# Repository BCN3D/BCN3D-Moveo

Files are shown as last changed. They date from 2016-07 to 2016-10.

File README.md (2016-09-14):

#BCN3D MOVEO

This is the repository that contains the CAD files, the STL files, the user manual (with the assembly manual), the firmware, and the Bill of Materials of the BCN3D Moveo.
BCN3D Technologies keeps taking important steps in order to achieve his goal of bringing the digital manufacturing technology to everyone. In this occasion we are presenting the BCN3D Moveo, a robotic arm design from scratch and developed by our engineers in collaboration with the Departament d’Ensenyament from the Generalitat de Catalunya. Its structure is fully printed using additive manufacturing technologies and its electronics are controlled by the software Arduino.
Moveo, fully functional nowadays, has been born, as all the BCN3D Technologies products, with an open and educational wish.

##Why BCN3D Moveo

One of the Departament d’Ensenyament worries is the high price of the materials the grade students must use on their internships. Holding that in mind, an Open Source robotic arm, adaptable by the students and low cost reproducible could take several educational itineraries: mechanical design, automatism, industrial programing, etc.
Thus, the BCN3D Moveo should allow the educational centers to enjoy a modifiable and easily accessible for the students, at a price far lower than the usual industrial equipment they used to have to acquire, with enough output for training purposes.
As a Fundació CIM area, BCN3D Technologies shares its educational vocation. That is the reason why when the Departament d’Ensenyament contacted us in order to suggest and offer this project a year ago we didn’t hesitate on taking that opportunity.
Once we had the robotic arm designed and manufactured we started the last phase of the project, which consisted on an assembling and fine tuning workshop for 15 institutes around Catalonia, which took place in the BCN3D Technologies.
These institutes already have the BCN3D Moveo in their classrooms and workshops, and will have to present an internship program that proves their knowledge about the arm during September.

##Open Source Technology: Github

As we have done with all our developed produtcs, the BCN3D Moveo files will be available for everyone. Thanks to the platform Github, a website where users around the world share their designs, anyone will be able to obtain all the necessary information in order to assemble his own BCN3D Moveo at home.

Unlike the other BCN3D products, the Moveo won’t be commercialized. The project has been born and developed in order to make a move for the community progress starting from the Departament d’Ensenyament idea.
Nevertheless, BCN3D will fee all the Moveo know how on our Github account, as we have been doing with all the BCN3D Technologies products. Thus, the users will be able to find the bill of material (BOM), where all the needed components for the assembling of the arm come detailed, as the CAD designs, so anyone will be able to modify the BCN3D Moveo design as they wish.
Furthermore, the Github users will find the STL files for the structure printing and the assembling, fine tuning and firmware upload manuals, which will be available both in English and Spanish.

## Acknowledgements

This project is based on a project by [Andreas Hölldorfer](http://chaozlabs.blogspot.de/). You can see his original project on [Hackaday.io](https://hackaday.io/project/3800-3d-printable-robot-arm), [Github](https://github.com/4ndreas/BetaBots-Robot-Arm-Project/tree/master), [Youtube](https://www.youtube.com/channel/UCeFKz1UJUd5YuxS1ZikqYwA).

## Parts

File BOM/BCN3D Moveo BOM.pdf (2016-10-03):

BCN3D Moveo BOM.xlsx

1

BOM ID | BOM | QUANTITY
1 | Stepper Motor SM42HT47-1684 1,8º step, 1,6 A, 3600 g·cm | 1
2 | ARDUINO MEGA 2560 | 1
3 | Stepper Driver tb6560 | 6
4 | Power Supply 24V 320W | 1
5 | RAMPS V1.4 | 1
6 | Power converter 24V a 12V | 1
7 | Servo Motor 180§ 55G TORQUE=13KG/CM | 1
8 | Gear Ratio 5:1 Planetary Gearbox Nema 17 Stepper 17HS19-1684S-PG5 ( step 0,35º , 2Nm, 1,68A) | 1
9 | Nema 23, 112mm, Ø8mm flat shaft SM57HT112-3004A, step 1,8º, 3A,28Kg·cm | 2
10 | Stepper Motor SM35HT36-1004A, 1,8º step, 1A, 1400g·cm | 1
11 | Stepper Motor nema 17 SM42HT33-1334, 1,8º step, 1,33A, 2200 g·cm | 1
12 | Chrome steel smooth bar-134mm | 1
13 | Chrome steel smooth bar-114mm | 1
14 | Chrome steel smooth bar-80mm | 1
15 | Ball Bearing 608ZZ 8mm x 22mm x 7mm | 10
16 | Ball Bearing 625ZZ 5mm x 16mm x 5mm | 8
17 | Ball Bearing 624ZZ 4mm x 13mm x 5mm | 9
18 | Ball Bearing 623ZZ 3mm x 10mm x 4mm | 3
19 | Brass insert M4 | 3
20 | Brass insert M3 | 20
21 | Pulley T5, Bore 8mm, 14 tooth, 17mm width | 3
22 | Pulley T5, Bore 5mm, 10 tooth, 17 mm width | 2
23 | ROD BAR M8 L 42mm | 1
24 | ZCOUPLING STEEL 5 TO 8 mm rigid | 1
25 | Axial Fan DC 24V 80x80mm | 1
26 | Axial Fan DC 24V 50x50mm | 1
27 | Powwer supply cable IEC 1,8m | 1
28 | Cable USB 2.0 AM/BM 1,8m | 1
29 | Cable Ties | 10
30 | Selfoil bearing 5mm x 8mm x 10mm | 8
31 | Selfoil bearing 8mm x 12mm x 20mm | 2
32 | Wood Base - 550mm x 550mm x 16mm | 1
33 | Breco belt T5, 16mm width, L 180cm | 1,8 m
101 | Dimension A: M-3 Dimension B: 10 mm | 30
102 | Dimension A: M-3 Dimension B: 12 mm | 6
103 | Dimension A: M-3 Dimension B: 16 mm | 13
104 | Dimension A: M-3 Dimension B: 20 mm | 4
105 | Dimension A: M-3 Dimension B: 25 mm | 5
106 | Dimension A: M-3 Dimension B: 30 mm | 2
107 | Dimension A: M-3 Dimension B: 40 mm | 7
108 | Dimension A: M-4 Dimension B: 12 mm | 2
109 | Dimension A: M-4 Dimension B: 10 mm | 2
110 | Dimension A: M-4 Dimension B: 16 mm | 8
111 | Dimension A: M-4 Dimension B: 40 mm | 4
112 | Dimension A: M-4 Dimension B: 45 mm | 6
113 | Dimension A: M-4 Dimension B: 60 mm | 4
114 | Dimension A: M-5 Dimension B: 14 mm | 120
115 | Dimension A: M-5 Dimension B: 20 mm | 8
116 | Dimension A: M-8 Dimension B: 65 mm | 1
117 | Dimension A: M-4 Dimension B: 25 mm | 4
118 | Dimension A: M-3 Nut | 30
119 | Dimension A: M-4 Nut | 4
120 | Dimension A: M-4 Locknut | 18
121 | Dimension A: M-5 Locknut | 16
122 | Dimension A: M-8 Locknut | 2

Components

Fasteners

BCN3D Moveo BOM.xlsx

2

123 | Dimension A: M-4 Dimension B: 20 mm | 3
124 | Dimension A: M-3 Dimension B: 8 mm | 4
125 | Dimension A: M-4 Dimension B: 30 mm | 8
126 | Dimension A: M-3 Dimension B: 35 mm | 4
127 | Washer M-3 | 10
| BOM ID | Parts | Name | Quantity
| 202 | Articulation 1 | 1M1 | 1
| 203 | | 1M2 | 1
| 204 | | 1M3 | 1
| 205 | Articulation 2 | 2M1 | 1
| 206 | | 2M2M | 1
| 207 | | 2M2H | 1
| 208 | | T2M1D | 1
| 209 | | T2M1I | 1
| 210 | Articulation 3 | 3M1 | 1
| 210A | | 3M2C | 1
| 211 | | 3M2 | 1
| 212 | | T3M1 | 1
| 213 | Articulation 4 | 4M1 | 1
| 214 | | 4M2 | 1
| 215 | | 4M2C | 1
| 216 | | T4M1 | 1
| 217 | Machine - tool | Top plate | 1
| 218 | | Bottom plate | 1
| 219 | | Cilinder | 2
| 220 | | Pivot arm | 1
| 221 | | Gripper left | 1
| 222 | | Gripper right | 1
| 223 | | Idol gear | 1
| 224 | | Servo gear | 1
| 225 | Box electronics | Box | 1
| 226 | | Fan module | 1
| 227 | | Suport Drivers | 1
| 228 | Base | Potes | 4
| 229 | Cover | Tapa 2M1 | 2
| 230 | | Tapa 3M1 | 2
| 231 | | Tapa 4M1 | 2
| 232 | | Tapa TBB | 1

Printed Parts

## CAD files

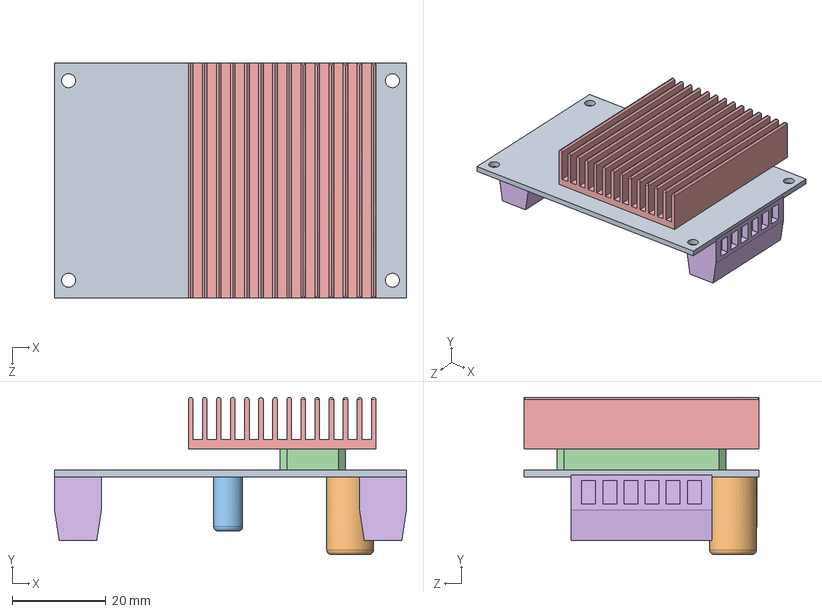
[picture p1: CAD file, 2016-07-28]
CAD files/Driver.SLDASM
75.0 x 33.5 x 50.0 mm
PCB TB6560
Capacitor 1
Capacitor 2
Chip
Sink
Terminal x 2

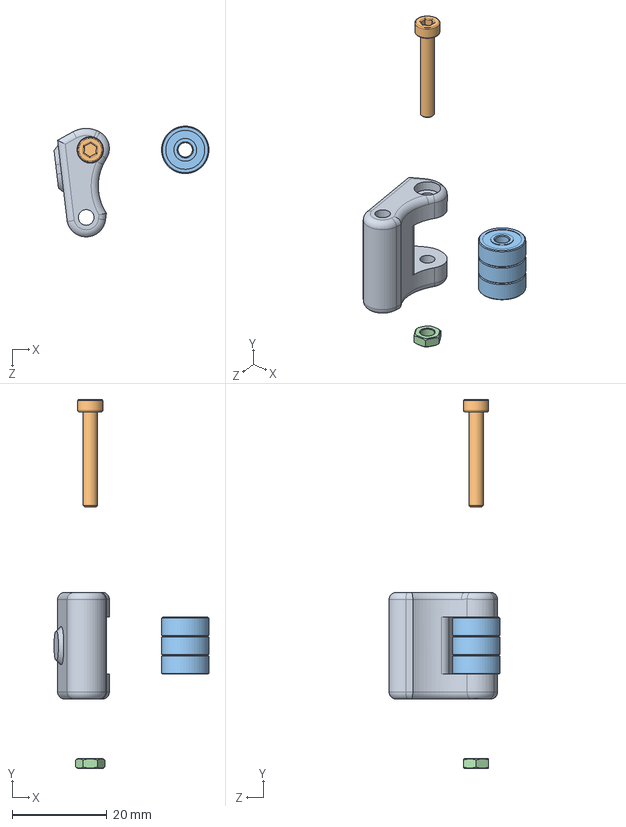
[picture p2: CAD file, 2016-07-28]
CAD files/M1 Tensor D.SLDASM
32.6 x 77.7 x 23.3 mm
T4M1E
M3x20
Bearing 3Bore 10Ext 4Height x 3
M3 Nut

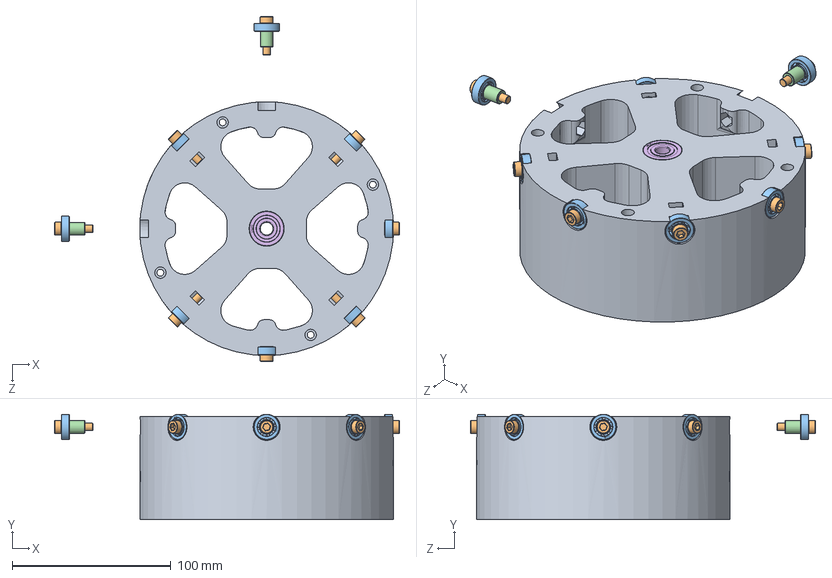
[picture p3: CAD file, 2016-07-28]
CAD files/Rotary Plate.SLDASM
217.5 x 66.5 x 217.5 mm
1M2A
M5x20 x 8
Bearing 5mm x 8
Spacer M5x10 x 8
Spacer M8x20
8mm Bearing x 2

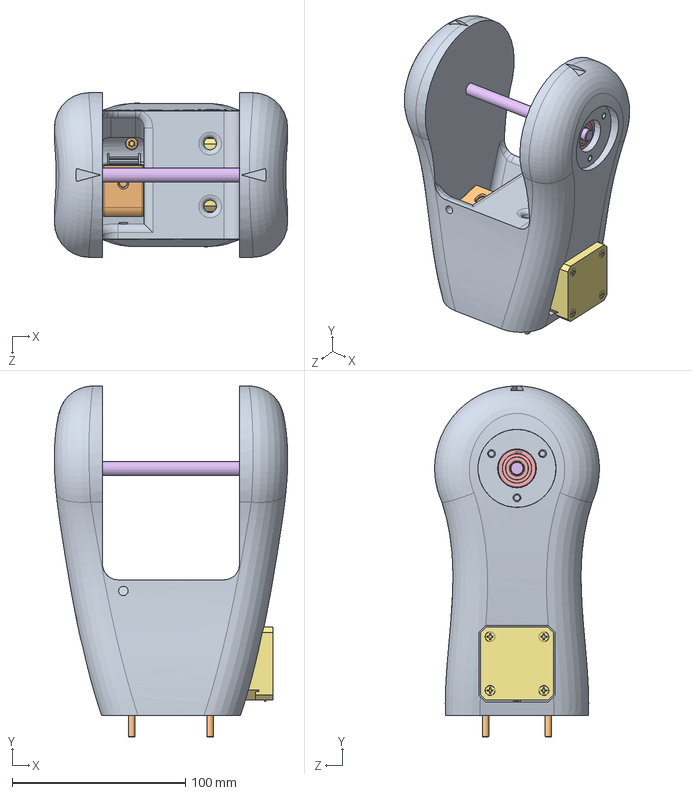
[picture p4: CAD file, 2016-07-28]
CAD files/3M1.SLDASM
134.6 x 202.4 x 95.0 mm
3M1D
T3M1C
M4 Nut
M4x20
Bearing 4Bore 13Ext 5 x 3
M3x40
Nema 17 Reductor
M3x12 x 4
Pulley 8mm IGNIS
M4x16 x 4
M3 Nut
Brass insert M3 x 6
8mm Bearing x 2
Smooth bar 8mm x 121mm

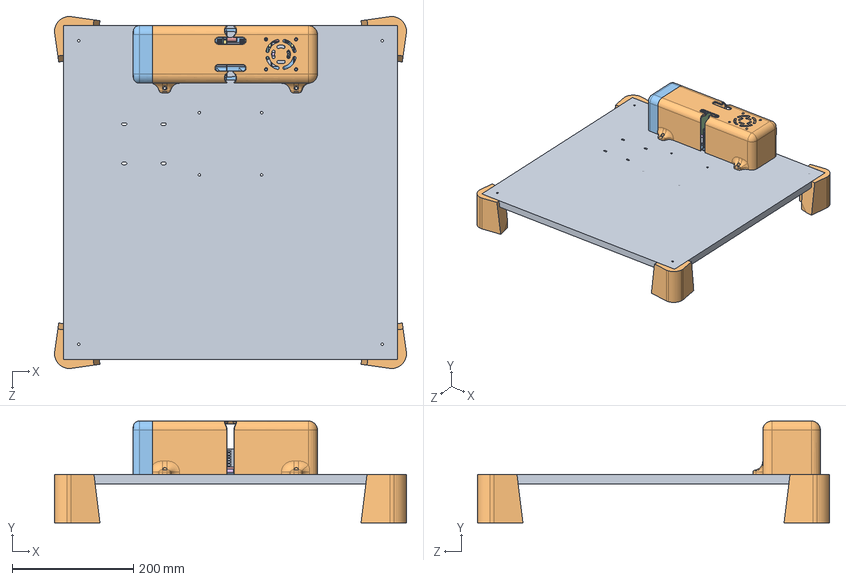
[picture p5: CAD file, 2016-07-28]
CAD files/Base assembly.SLDASM
579.8 x 168.0 x 579.8 mm
Base fusta
Potes base B x 4
Suport Drivers E
PCB TB6560 x 6
Capacitor 1 x 6
Capacitor 2 x 6
Chip x 6
Sink x 6
Terminal x 12
Box C
Fan Module
Fan

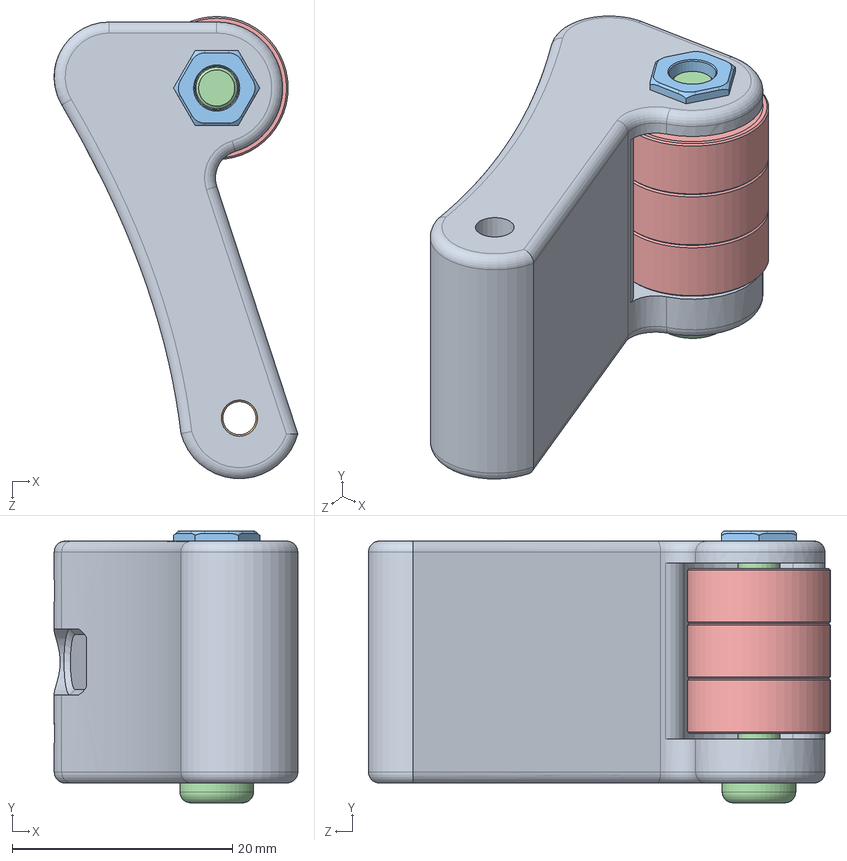
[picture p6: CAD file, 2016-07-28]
CAD files/Tensor I.SLDASM
22.2 x 24.7 x 42.0 mm
T2M1BI
M3 Nut
M4 Nut
M4x20
Bearing 4Bore 13Ext 5 x 3

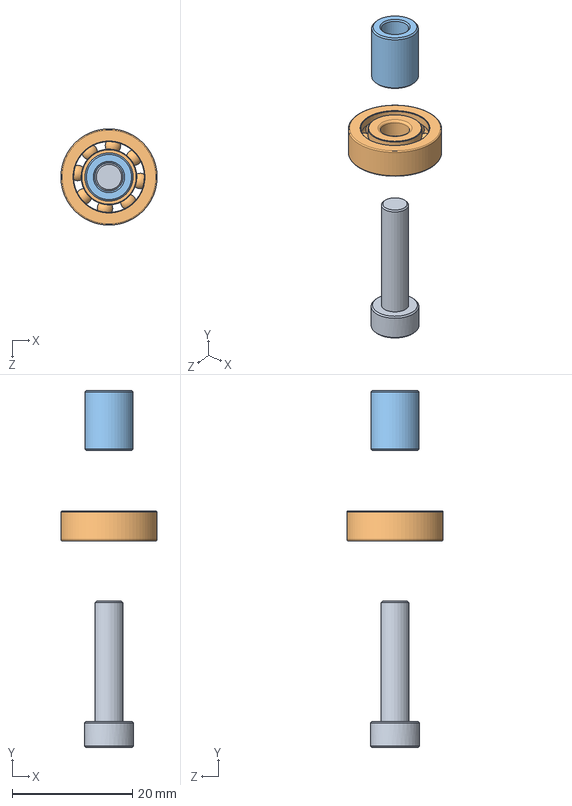
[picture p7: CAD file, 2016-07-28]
CAD files/Sistema rodaments.SLDASM
16.0 x 59.3 x 16.0 mm
M5x20
Bearing 5mm
Spacer M5x10

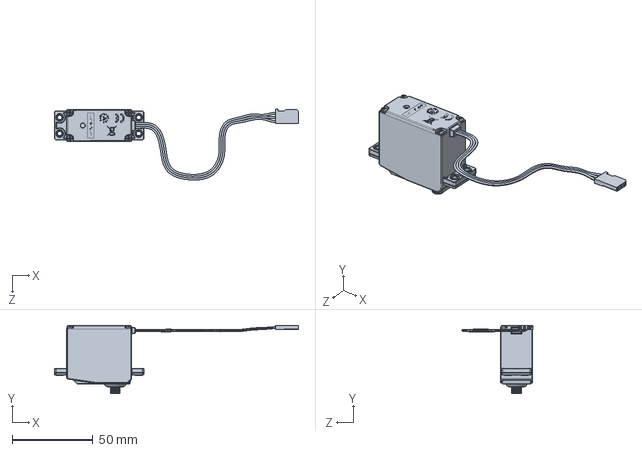
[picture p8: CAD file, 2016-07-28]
CAD files/2.SLDASM
151.2 x 42.3 x 44.1 mm

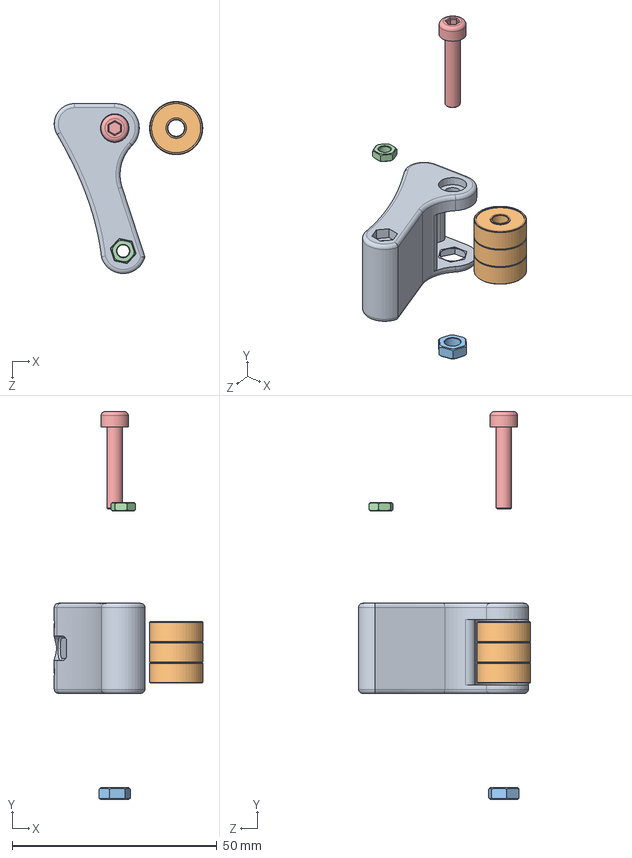
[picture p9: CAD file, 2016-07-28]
CAD files/Tensor D.SLDASM
36.3 x 94.7 x 42.0 mm
T2M1BD
Bearing 4Bore 13Ext 5 x 3
M4 Nut
M3 Nut
M4x20
Arandela

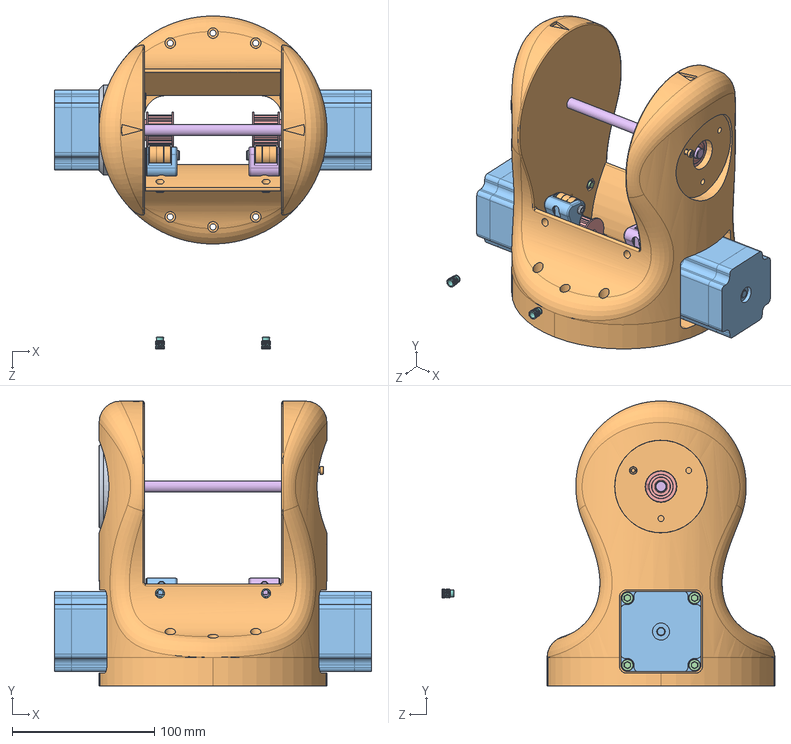
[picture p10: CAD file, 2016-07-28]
CAD files/2M1 assembly.SLDASM
222.5 x 200.0 x 233.7 mm
M5 Lock x 8
2M1D
Nema 23 x 2
M5x15 x 8
8mm Bearing x 2
T2M1BI
M3 Nut x 2
M4 Nut x 2
M4x20 x 2
Bearing 4Bore 13Ext 5 x 6
T2M1BD
Arandela
Pulley 8mm IGNIS x 2
Smooth bar 8mm x 140mm
Brass insert M4 x 2

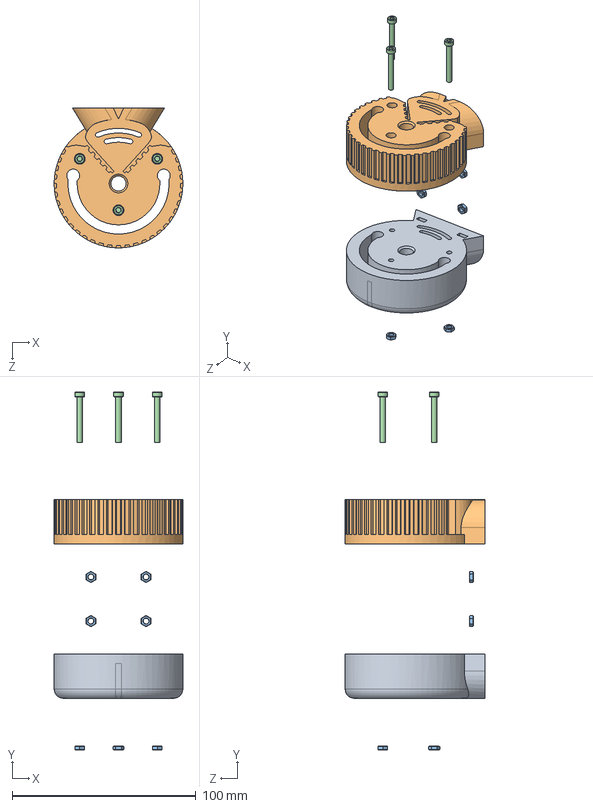
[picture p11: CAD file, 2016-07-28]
CAD files/4M2.SLDASM
70.0 x 194.7 x 76.0 mm
4M2B
4M2CB
M3 Nut x 7
M3x25 x 3

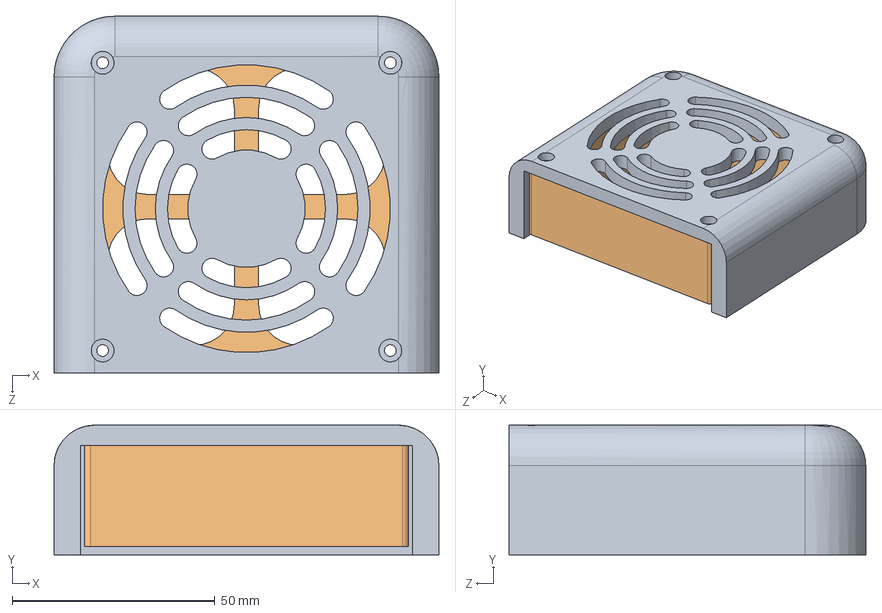
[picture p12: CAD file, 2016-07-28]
CAD files/Module Fan Assembly.SLDASM
95.0 x 32.0 x 88.0 mm
Fan Module
Fan

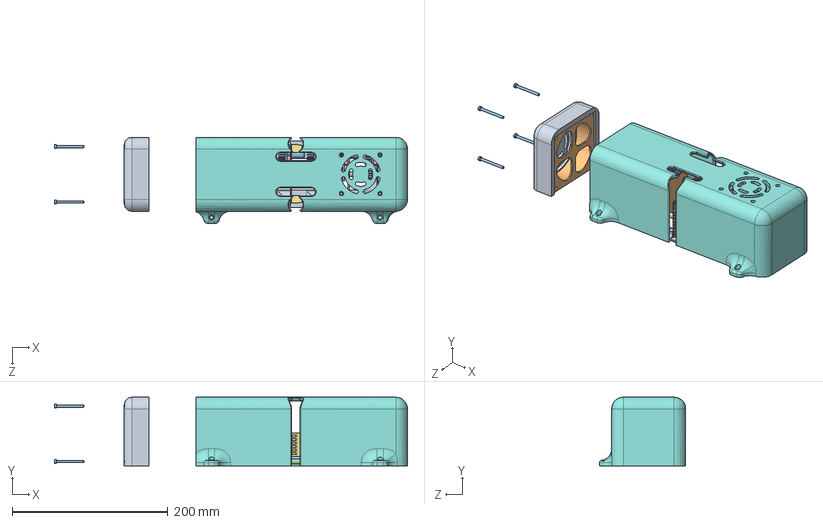
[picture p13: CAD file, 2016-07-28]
CAD files/Box Assembly B.SLDASM
453.0 x 88.0 x 111.0 mm
Suport Drivers E
PCB TB6560 x 6
Capacitor 1 x 6
Capacitor 2 x 6
Chip x 6
Sink x 6
Terminal x 12
Box C
Fan Module
Fan
M3x35 x 4

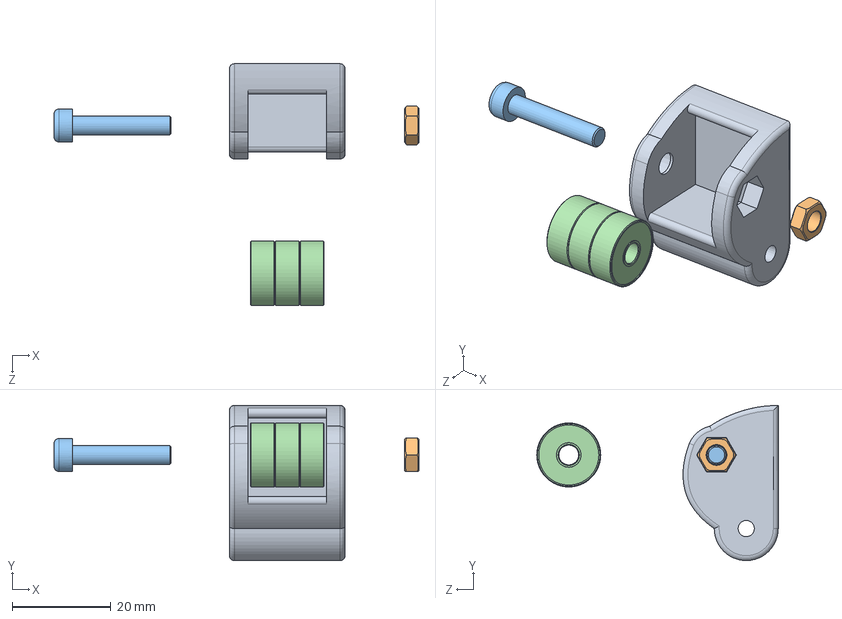
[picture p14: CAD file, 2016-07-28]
CAD files/T3M1.SLDASM
74.1 x 31.5 x 49.0 mm
T3M1C
M4 Nut
M4x20
Bearing 4Bore 13Ext 5 x 3

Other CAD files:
CAD files/2M2 assembly.SLDASM
CAD files/Drivers Support Assembly B.SLDASM
CAD files/2M2.SLDASM
CAD files/Gripper B Assembly.SLDASM
CAD files/1M1B.SLDPRT
CAD files/1M2A.SLDPRT
CAD files/1M3.SLDASM
CAD files/1M3A.SLDPRT
CAD files/2M1D.SLDPRT
CAD files/2M2HA.SLDPRT
CAD files/2M2M assembly.SLDASM
CAD files/2M2MA.SLDPRT
CAD files/3M2C.SLDPRT
CAD files/3M2CC.SLDPRT
CAD files/4M1D.SLDPRT
CAD files/4M2B.SLDPRT
CAD files/4M2CB.SLDPRT
CAD files/8mm Bearing.SLDPRT
CAD files/Arandela.SLDPRT
CAD files/Barra llisa 8mm x 80mm.SLDPRT
CAD files/Base fusta.SLDPRT
CAD files/Bearing 3Bore 10Ext 4Height.SLDPRT
CAD files/Bearing 4Bore 13Ext 5.SLDPRT
CAD files/Bearing 5mm.SLDPRT
CAD files/Bottom Plate C.SLDPRT
CAD files/Box C.SLDPRT
CAD files/Brass insert M3.SLDPRT
CAD files/Brass insert M4.SLDPRT
CAD files/Capacitor 1.SLDPRT
CAD files/Capacitor 2.SLDPRT
CAD files/Chip.SLDPRT
CAD files/Cilinder.SLDPRT
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

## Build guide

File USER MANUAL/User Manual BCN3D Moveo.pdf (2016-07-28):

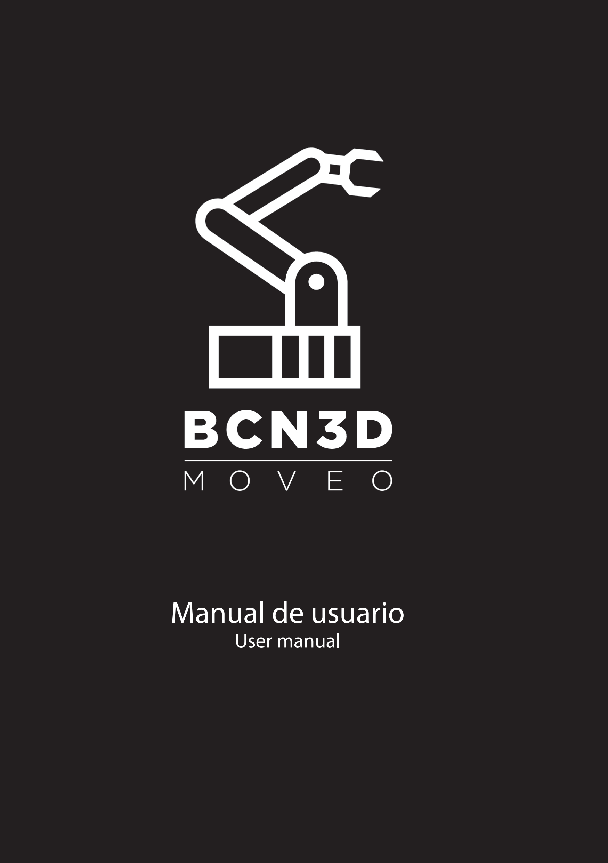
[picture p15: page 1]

# Manual de usuario

# User manual

2 - Manual de usuario User manual

Manual de montaje
Assembly manual

Manual de usuario User manual

¿Cómo usar el BCN3D Moveo? How to use the BCN3D Moveo?

Instalación del firmware
Firmware installation

Sobre el BCN3D Moveo
About de BCN3D Moveo

## ÍNDICE INDEX

3 - 4

6 - 39

40 - 42

43 - 45

Manual de usuario User manual - 3

## Sobre el BCN3D Moveo About the BCN3D Moveo

BCN3D Technologies sigue dando pasos importantes para cumplir con su objetivo de acercar las tecnologías de fabricación digital y aditiva al público general. En esta ocasión queremos presentar el BCN3D Moveo, un brazo robótico diseñado desde cero y desarrollado por nuestros ingenieros en colaboración con el Departament d’Ensenyament de la Generalitat de Catalunya, cuya estructura está impresa en 3D y su tecnología controlada por el software Arduino.
Moveo, totalmente funcional a día de hoy, ha nacido, como todos los demás productos salidos de BCN3D Technologies, con voluntad formativa y abierta.

EL PORQUÉ DE BCN 3D MOVEO

Una de las preocupaciones del Departament d’Ensenyament es el elevado coste de los materiales que deben usar los alumnos de formación de grado para realizar sus prácticas. En este sentido, un brazo robótico Open Source, modificable por los alumnos y reproducible a bajo coste podía copar varios de los itinerarios formativos existentes: Diseño mecánico, automatismos, programación industrial, etc.
Así pues, el BCN3D Moveo debería permitir a los institutos disfrutar de un equipamiento personalizable, modificable y de fácil acceso para el alumno a un precio lejos de los equipamientos industriales que normalmente habían tenido que adquirir, pero con unas prestaciones suficientes para los fines formativos.
Como área de la Fundació CIM, BCN3D Technologies comparte la vocación formativa de su alma máter. Es por dicho motivo que cuando el Departament d’Ensenyament se puso en contacto con nosotros para proponernos el proyecto un año atrás, no dudamos en aceptar la propuesta.
Una vez tuvimos el brazo diseñado y fabricado, se inició la última parte del proyecto que consistía en un workshop de montaje y puesta en marcha para 15 institutos de Cataluña, realizado en las instalaciones de BCN3D Technologies.
Estos institutos ya cuentan con el BCN3D Moveo en sus aulas y talleres, y deberán presentar prácticas que acrediten su conocimiento del equipo durante el mes de setiembre.

BCN3D Technologies keeps taking important steps in order to achieve his goal of bringing the digital manufacturing technology to everyone. In this occasion we are presenting the BCN3D Moveo, a robotic arm design from scratch and developed by our engineers in collaboration with the Departament d’Ensenyament from the Generalitat de Catalunya. Its structure is fully printed using additive manufacturing technologies and its electronics are controlled by the software Arduino.
Moveo, fully functional nowadays, has been born, as all the BCN3D Technologies products, with an open and educational wish.

WHY BCN 3D MOVEO

One of the Departament d’Ensenyament worries is the high price of the materials the grade students must use on their internships. Holding that in mind, an Open Source robotic arm, adaptable by the students and low cost reproducible could take several educational itineraries: mechanical design, automatism, industrial programing, etc.
Thus, the BCN3D Moveo should allow the educational centers to enjoy a modifiable and easily accessible for the students, at a price far lower than the usual industrial equipment they used to have to acquire, with enough output for training purposes. As a Fundació CIM area, BCN3D Technologies shares its educational vocation. That is the reason why when the Departament d’Ensenyament contacted us in order to suggest and offer this project a year ago we didn’t hesitate on taking that opportunity. Once we had the robotic arm designed and manufactured we started the last phase of the project, which consisted on an assembling and fine tuning workshop for 15 institutes around Catalonia, which took place in the BCN3D Technologies.
These institutes already have the BCN3D Moveo in their classrooms and workshops, and will have to present an internship program that proves their knowledge about the arm during September.

## Sobre el BCN3D Moveo About the BCN3D Moveo

TECNOLOGÍA OPEN SOURCE: LA PLATAFORMA
GITHUB

Como hiciéramos con todos nuestros productos, los archivos del BCN3D Moveo estarán a la disposición de todo aquel que quiera acceder a ellos. Gracias a la plataforma Github, un espacio en el que los usuarios comparten sus diseños de forma libre, cualquier persona podrá obtener toda la información necesaria para montarse su propio BCN3D Moveo en casa.
A diferencia de los otros productos de BCN3D Technologies, el BCN3D Moveo no será comercializado. El proyecto se ha realizado con el ánimo de dar una aportación más a la comunidad a partir de la idea del Departament d’Ensenyament.
BCN3D liberará el conocimiento del Moveo en sus repositorios en Github como se ha venido haciendo con los productos oficiales de BCN3D Techologies. De esta manera, se espera que la comunidad y los centros formativos que estén interesados puedan fabricar sus propios robots.
Así, entre los archivos que subiremos a dicha plataforma incluimos el “bill of materials” (BOM), en el que se detallan todos los componentes necesarios para montar el brazo, así como los diseños CAD, para que todo el mundo pueda modificar el diseño del BCN3D Moveo a su gusto. De la misma forma, los usuarios de Github podrán encontrar los archivos STL para la impresión de la estructura del brazo, y el manual de montaje del mismo que estará en español e inglés.
Gracias a este proyecto impulsado por el Departament d’Ensenyament y desarrollado por BCN3D Technologies, todo el mundo podrá fabricarse un brazo robótico en casa, sin necesidad de tener un amplio conocimiento técnico. Así, os animamos a todos a fabricaros el BCN3D Moveo y compartir los resultados en las redes con el hashtag #BCN3DMoveo.

OPEN SOURCE TECHNOLOGY: GITHUB

As we have done with all our developed pordutcs, the BCN3D Moveo files will be available for everyone. Thanks to the platform Github, a website where users around the world share their designs, anyone will be able to obtain all the necessary information in order to assemble his own BCN3D Moveo at home.
Unlike the other BCN3D products, the Moveo won’t be commercialized. The project has been born and developed in order to make a move for the community progress starting from the Departament d’Ensenyament idea.
Nevertheless, BCN3D will fee all the Moveo know how on our Github account, as we have been doing with all the BCN3D Technologies products. Thus, the users will be able to find the bill of material (BOM), where all the needed components for the assembling of the arm come detailed, as the CAD designs, so anyone will be able to modify the BCN3D Moveo design as they wish.
Furthermore, the Github users will find the STL files for the structure printing and the assembling, fine tuning and firmware upload manuals, which will be available both in English and Spanish.
Thanks to this project motivated by the Departament d’Ensenyament and developed by BCN3D Technologies everyone will be able to fabricate their own robotic arm at home, no highly technical knowledge needed. Therefore, we encourage you to fabricate the BCN3D Moveo and share the results on the social networks using the hashtag #BCN3DMoveo.

# Manual de montaje

# Assembly manual

## Montaje del módulo 1 Module 1

x8

BOM | Descripción Description | Cant Qty
115 | Tornillo M5 x 20mm Screw M5 x 20mm | 8
16 | Rodamiento 5mm x 16mm x 5mm Bearing 5mm x 16mm x 5mm | 8
30 | Espaciador 5mm x 10mm Spacer 5mm x 10mm | 8

121 | Tuerca autoblocante M5 M5 locknut | 8
15 | Rodamiento 8mm x 22mm x 7mm Bearing 8mm x 22mm x 7mm | 2
- | 1M2A Base rotatoria 1M2A Rotary plate | 1

## Montaje del módulo 1 Module 1 assembly

x1

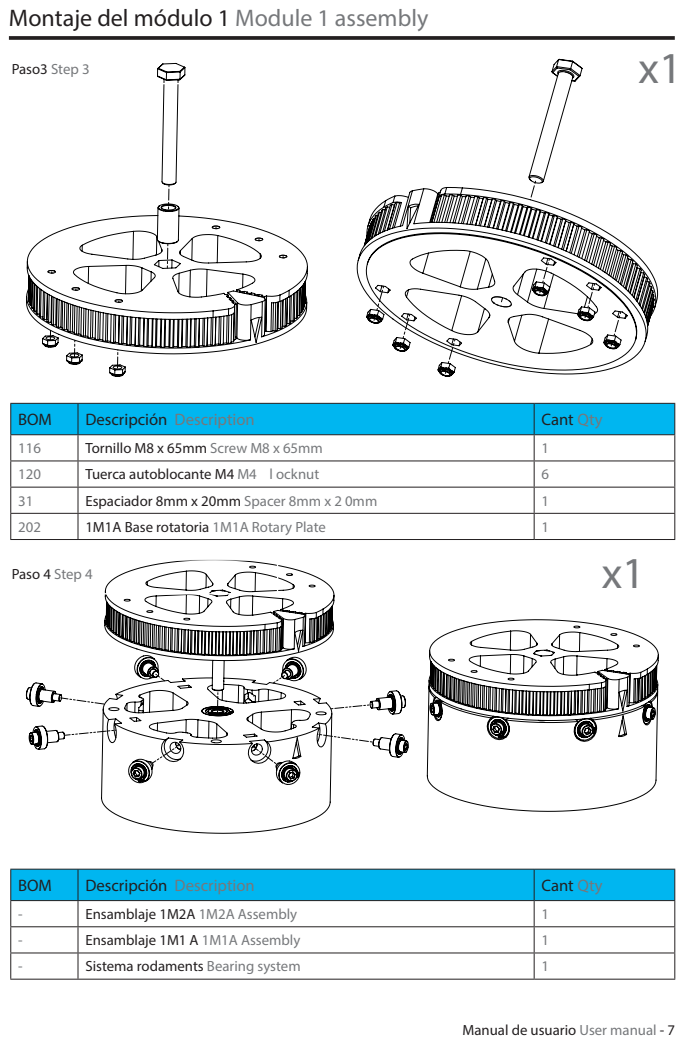
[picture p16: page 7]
Paso3 Step 3; Paso 4 Step 4

BOM | Descripción Description | Cant Qty
116 | Tornillo M8 x 65mm Screw M8 x 65mm | 1
120 | Tuerca autoblocante M4 M4 l ocknut | 6
31 | Espaciador 8mm x 20mm Spacer 8mm x 2 0mm | 1
202 | 1M1A Base rotatoria 1M1A Rotary Plate | 1

- | Ensamblaje 1M2A 1M2A Assembly | 1
- | Ensamblaje 1M1 A 1M1A Assembly | 1
- | Sistema rodaments Bearing system | 1

## Montaje del módulo 1 Module 1 assembly

BOM ID | Descripción Description | Cant Qty
204 | Pieza impresa 1M3 Printed part 1M3 | 1
1 | Motor nema 17 largo Large nema 17 motor | 1
101 | Tornillo M3 x 10mm M3 x 8mm screw | 4
22 | Polea 5mm 5mm pulley | 1

## Montaje del módulo 2 Module 2 assembly

x1

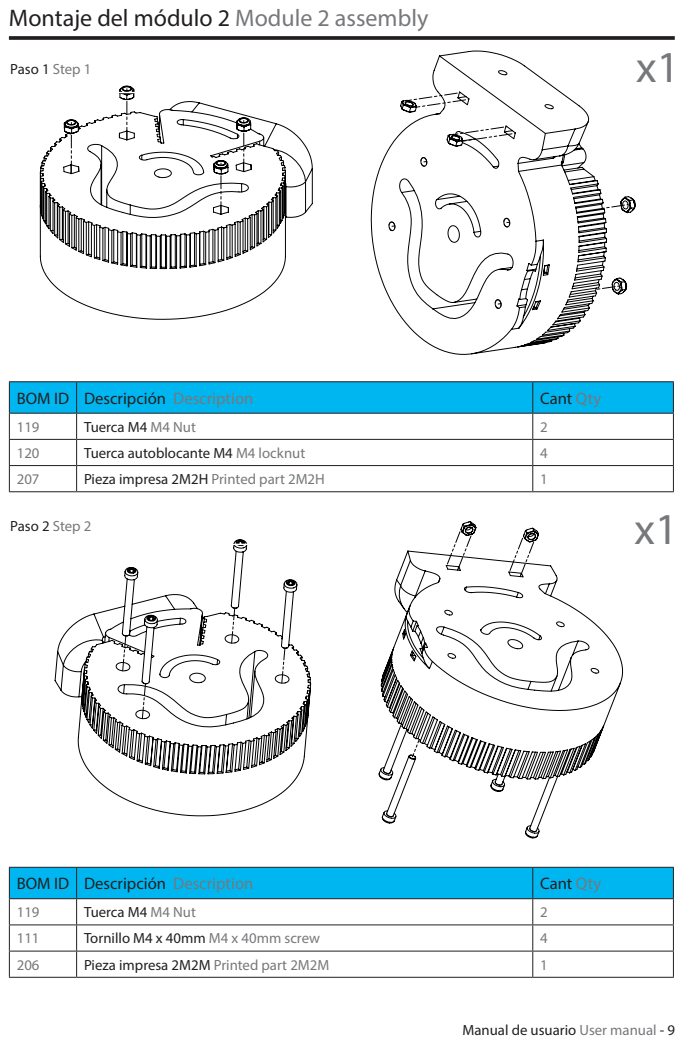
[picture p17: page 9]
Paso 1 Step 1; Paso 2 Step 2

BOM ID | Descripción Description | Cant Qty
119 | Tuerca M4 M4 Nut | 2
120 | Tuerca autoblocante M4 M4 locknut | 4
207 | Pieza impresa 2M2H Printed part 2M2H | 1

111 | Tornillo M4 x 40mm M4 x 40mm screw | 4
206 | Pieza impresa 2M2M Printed part 2M2M | 1

## Montaje del módulo 2 Module 2 assembly

BOM ID | Descripción Description | Cant Qty
- | Ensamblaje 2M2H 2M2H assembly | 2
- | Ensamblaje 2M2M 2M2M assembly | 2

## Montaje del módulo 2 Module 2 assembly

x1

BOM ID | Descripción Description | Cant Qty
208 | Pieza impresa T2M1D Printed part T2M1D | 1
117 | Tornillo M4 x 20mm M4 x 20mm screw | 1
119 | Tuerca M4 M4 nut | 1
118 | Tuerca M3 M3 nut | 1
17 | Rodamiento 4mm x 13mm x 5mm Bearing 4mm x 13mm x 5mm | 3

209 | Pieza impresa T2M1I Printed part T2M 1I | 1

## Montaje del módulo 2 Module 2 assembly

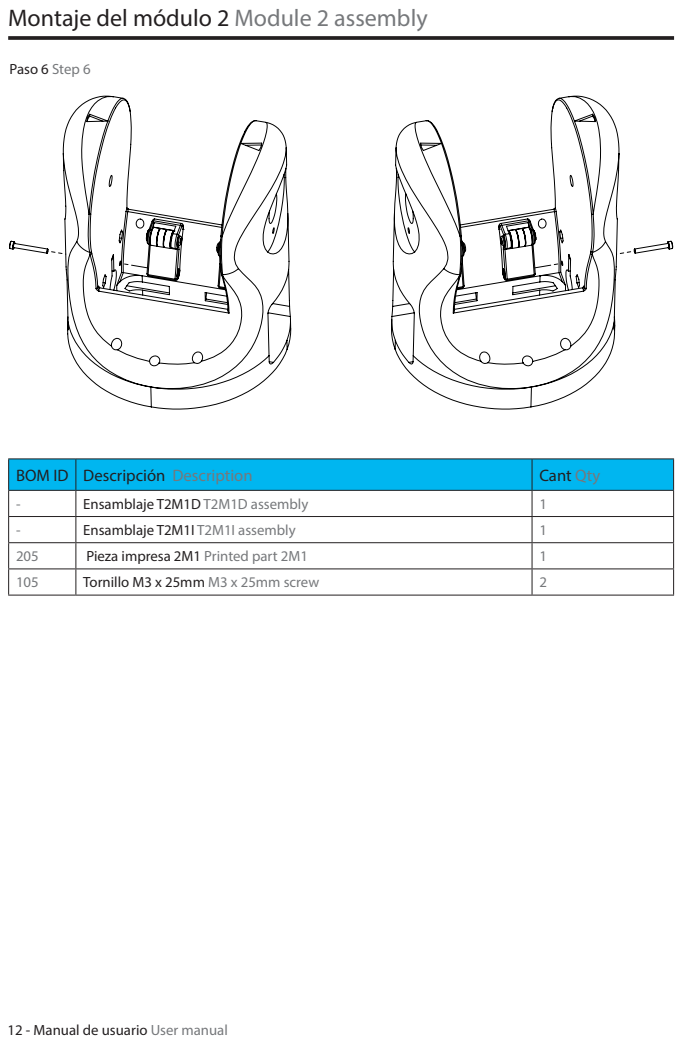
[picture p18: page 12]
Paso 6 Step 6

BOM ID | Descripción Description | Cant Qty
- | Ensamblaje T2M1D T2M1D assembly | 1
- | Ensamblaje T2M1I T2M1I assembly | 1
205 | Pieza impresa 2M1 Printed part 2M1 | 1
105 | Tornillo M3 x 25mm M3 x 25mm screw | 2

## Montaje del módulo 2 Module 2 assembly

BOM ID | Descripción Description | Cant Qty
9 | Motor Nema 23 Nema 23 motor | 2
114 | Tornillo M5 x 14mm M5 x 14mm screw | 8
121 | Tuerca autoblocante M5 M5 locknut | 8

## Montaje del módulo 2 Module 2 assembly

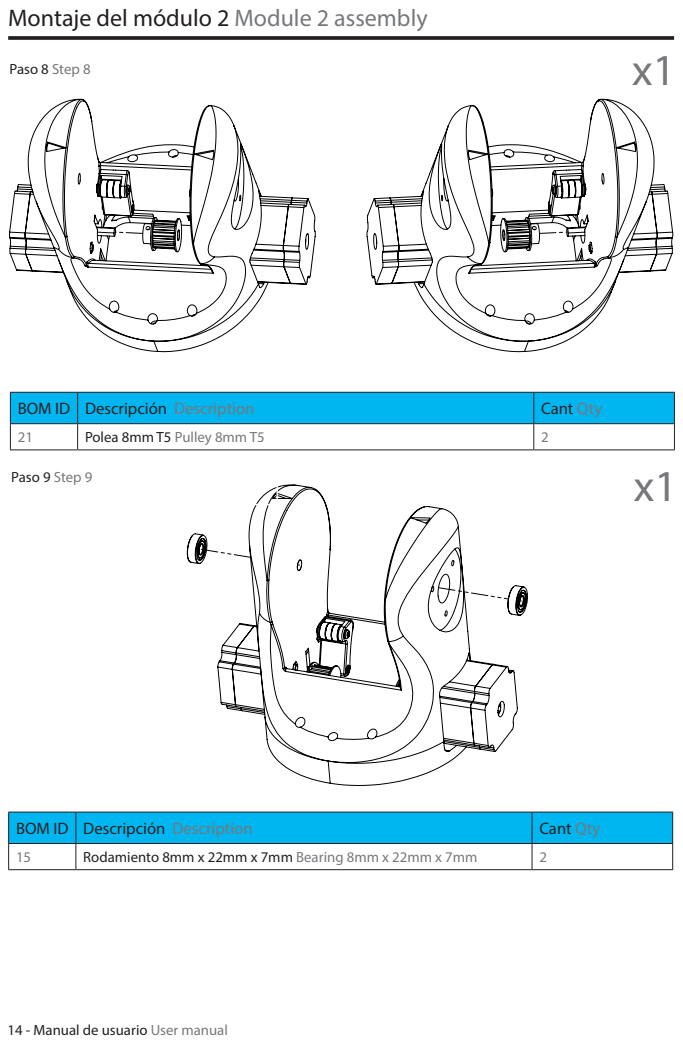
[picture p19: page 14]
Paso 8 Step 8; Paso 9 Step 9

BOM ID | Descripción Description | Cant Qty
21 | Polea 8mm T5 Pulley 8mm T5 | 2

15 | Rodamiento 8mm x 22mm x 7mm Bearing 8mm x 22mm x 7mm | 2

## Montaje del módulo 2 Module 2 assembly

BOM ID | Descripción Description | Cant Qty
- | Ensamblaje 2M2 2M2 assembly | 1

12 | Barra lisa 134mm Smooth bar 134mm | 1

## Montaje del módulo 2 Module 2 assembly

BOM ID | Descripción Description | Cant Qty
19 | Inserto M4 M4 insert | 2

20 | Inserto M3 M3 insert | 2
101 | Tornillo M3 x 10mm M3 x 10mm screw | 6
229 | Pieza impresa Tapa 2M1 Printed part Tapa 2M1 | 1

## Montaje de la herramienta Tool assembly

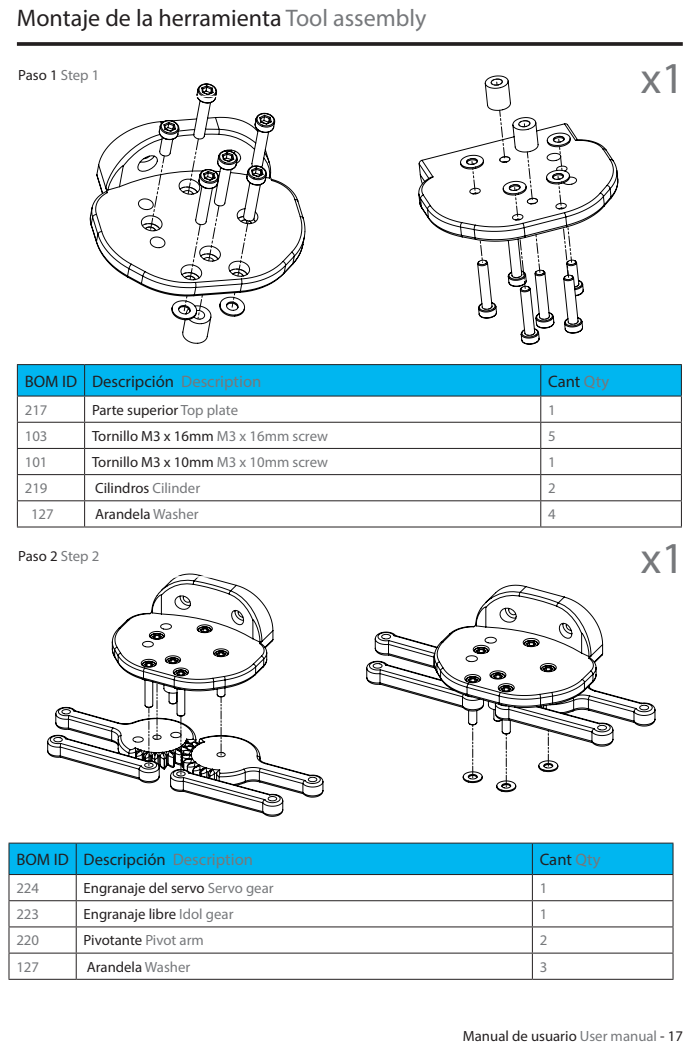
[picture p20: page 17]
Paso 1 Step 1; Paso 2 Step 2

BOM ID | Descripción Description | Cant Qty
217 | Parte superior Top plate | 1
103 | Tornillo M3 x 16mm M3 x 16mm screw | 5
101 | Tornillo M3 x 10mm M3 x 10mm screw | 1
219 | Cilindros Cilinder | 2
127 | Arandela Washer | 4

224 | Engranaje del servo Servo gear | 1
223 | Engranaje libre Idol gear | 1
220 | Pivotante Pivot arm | 2
127 | Arandela Washer | 3

## Montaje de la herramienta Tool assembly

BOM ID | Descripción Description | Cant Qty
218 | Parte inferior Bottom plate | 1
118 | Tuerca M3 M3 nut | 4

221 | Pinza izquiera Left gripper | 1
222 | Pinza derecha Right gripper | 1
103 | Tornillo M3 x 16mm M3 x 16mm screw | 8

## Montaje del módulo 3 Module 3 assembly

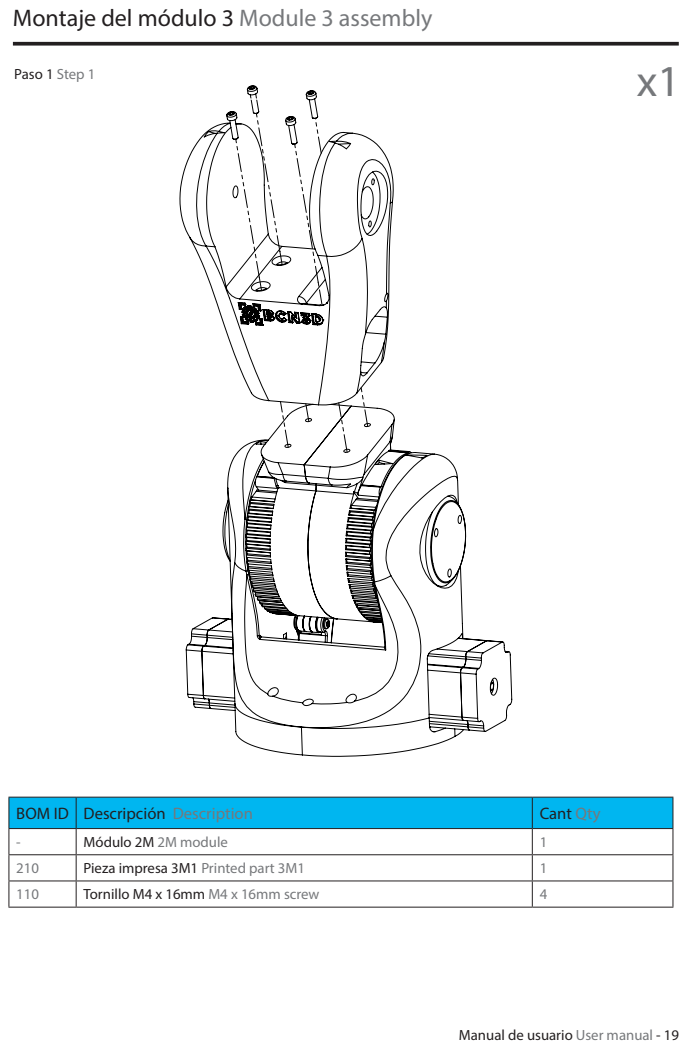
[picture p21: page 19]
Paso 1 Step 1

BOM ID | Descripción Description | Cant Qty
- | Módulo 2M 2M module | 1
210 | Pieza impresa 3M1 Printed part 3M1 | 1
110 | Tornillo M4 x 16mm M4 x 16mm screw | 4

## Montaje del módulo 3 Module 3 assembly

BOM ID | Descripción Description | Cant Qty
212 | Pieza impresa T3M1 Printed part T3M1 | 1
17 | Rodamiento 4mm x 13mm x 5mm Bearing 4mm x 13mm x 5mm | 3
123 | Tornillo M4 x 20mm M4 x 20mm screw | 1
119 | Tuerca M4 M4 nut | 1

- | Módulo T3M1 T3M1 module | 1
107 | Tornillo M3 x 40mm M3 x 40mm screw | 1
118 | Tuerca M3 M3 nut | 1

## Montaje del módulo 3 Module 3 assembly

BOM ID | Descripción Description | Cant Qty
210A | Pieza impresa 3M2C Printed part 3M2C | 1
11 | Motor Nema-17 34mm Nema-17 motor 34mm | 1
101 | Tornillo M3 x 10mm M3 x 10mm screw | 2

24 | Acoplador 8mm - 5mm Coupling 8mm- 5mm | 1
23 | Barra roscada 42mm Rod bar 42mm | 1
15 | Rodamiento 8mm x 22mm x 7mm Bearing 8mm x 22mm x 7mm | 1

## Montaje del módulo 4 Module 4 assembly

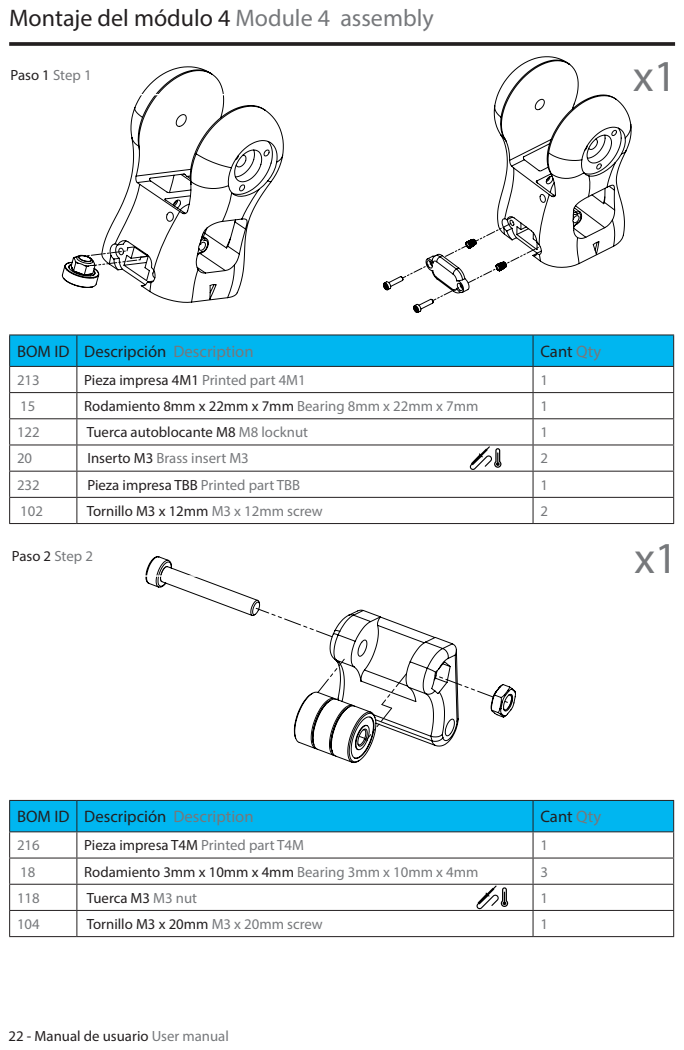
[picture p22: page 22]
Paso 1 Step 1; Paso 2 Step 2

BOM ID | Descripción Description | Cant Qty
213 | Pieza impresa 4M1 Printed part 4M1 | 1
15 | Rodamiento 8mm x 22mm x 7mm Bearing 8mm x 22mm x 7mm | 1
122 | Tuerca autoblocante M8 M8 locknut | 1
20 | Inserto M3 Brass insert M3 | 2
232 | Pieza impresa TBB Printed part TBB | 1
102 | Tornillo M3 x 12mm M3 x 12mm screw | 2

216 | Pieza impresa T4M Printed part T4M | 1
18 | Rodamiento 3mm x 10mm x 4mm Bearing 3mm x 10mm x 4mm | 3
118 | Tuerca M3 M3 nut | 1
104 | Tornillo M3 x 20mm M3 x 20mm screw | 1

## Montaje del módulo 4 Module 4 assembly

BOM ID | Descripción Description | Cant Qty
214 | Pieza impresa 4M2 Printed part 4M2 | 1
215 | Pieza impresa 4M2C Printed part 4M2C | 1
118 | Tuerca M3 M3 nut | 3
117 | Tornillo M4 x 25mm M4 x 25mm screw | 2
120 | Tuerca autoblocante M4 M4 Locknut | 4

## Montaje del módulo 4 Module 4 assembly

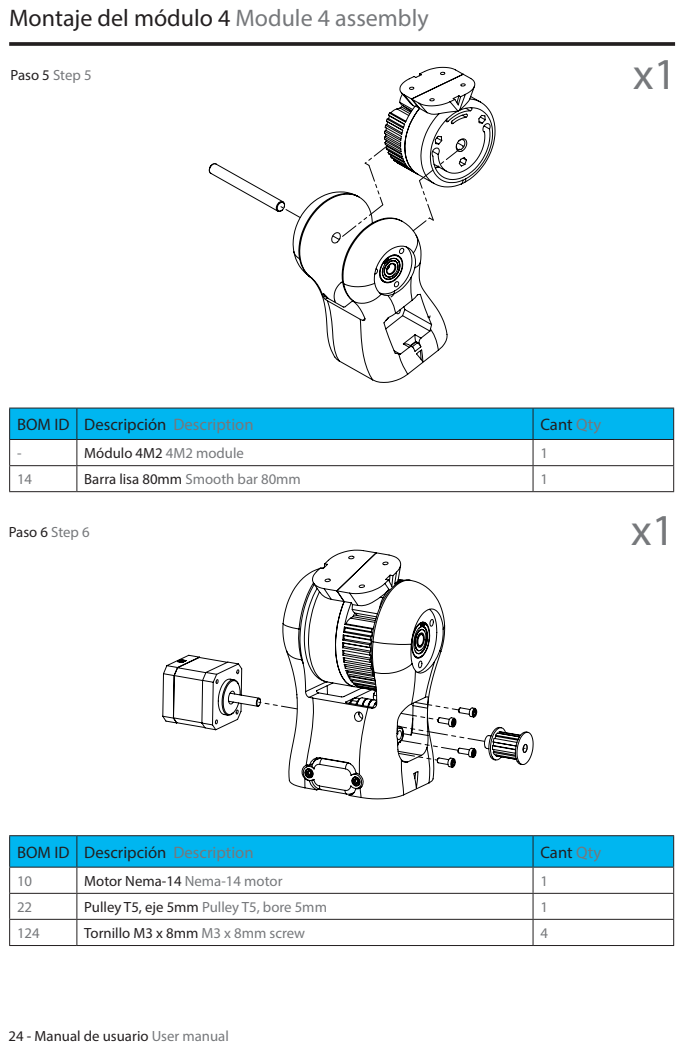
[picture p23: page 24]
Paso 5 Step 5; Paso 6 Step 6

BOM ID | Descripción Description | Cant Qty
- | Módulo 4M2 4M2 module | 1
14 | Barra lisa 80mm Smooth bar 80mm | 1

10 | Motor Nema-14 Nema-14 motor | 1
22 | Pulley T5, eje 5mm Pulley T5, bore 5mm | 1
124 | Tornillo M3 x 8mm M3 x 8mm screw | 4

## Montaje del módulo 4 Module 4 assembly

BOM ID | Descripción Description | Cant Qty
20 | Inserto M3 M3 insert | 6
231 | Pieza impresa Tapa 4M1 Printed part tapa 4M1 | 6
102 | Tornillo M3 x 12mm M3 x 12mm screw | 2

- | Módulo herramienta Tool module | 1
103 | Tornillo M3 x 16mm M3 x 16mm screw | 4

## Montaje del módulo 4 Module 4 assembly

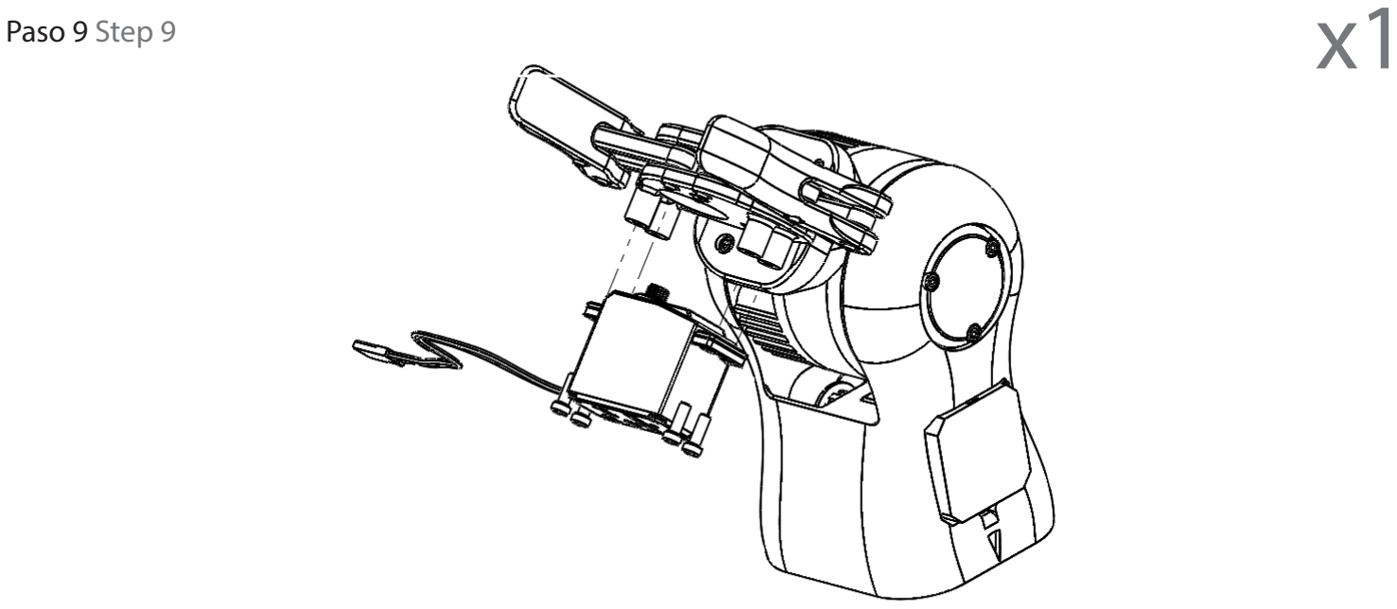
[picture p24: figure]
Paso 9 Step 9

BOM ID | Descripción Description | Cant Qty
7 | Servo motor Servo motor | 1
101 | Tornillo M3 x 10mm M3 x 10mm screw | 4

## Montaje del módulo 3 Module 3 assembly

BOM ID | Descripción Description | Cant Qty
- | Ensamblaje módulo 4 Tool module | 1
103 | Tornillo M3 x 16mm M3 x 16mm screw | 4

## Montaje del módulo 3 Module 3 assembly

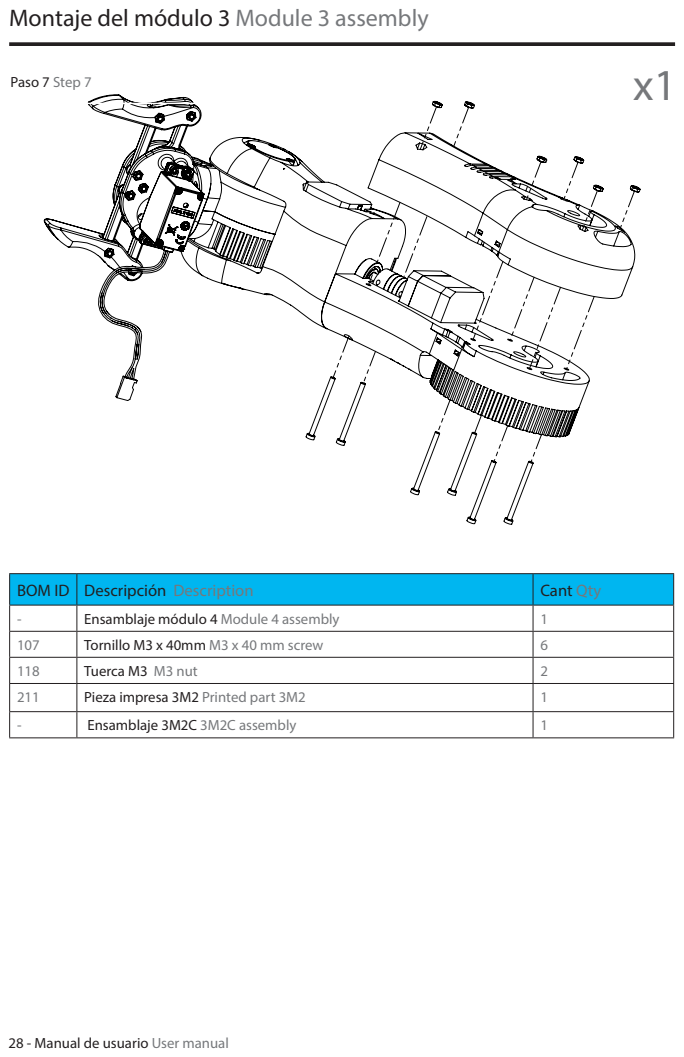
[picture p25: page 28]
Paso 7 Step 7

BOM ID | Descripción Description | Cant Qty
- | Ensamblaje módulo 4 Module 4 assembly | 1
107 | Tornillo M3 x 40mm M3 x 40 mm screw | 6
118 | Tuerca M3 M3 nut | 2
211 | Pieza impresa 3M2 Printed part 3M2 | 1
- | Ensamblaje 3M2C 3M2C assembly | 1

## Montaje del módulo 3 Module 3 assembly

BOM ID | Descripción Description | Cant Qty
15 | Rodamiento 8mm x 22mm x 7mm Bearing 8mm x 22mm x 7mm | 2

## Montaje del módulo 3 Module 3 assembly

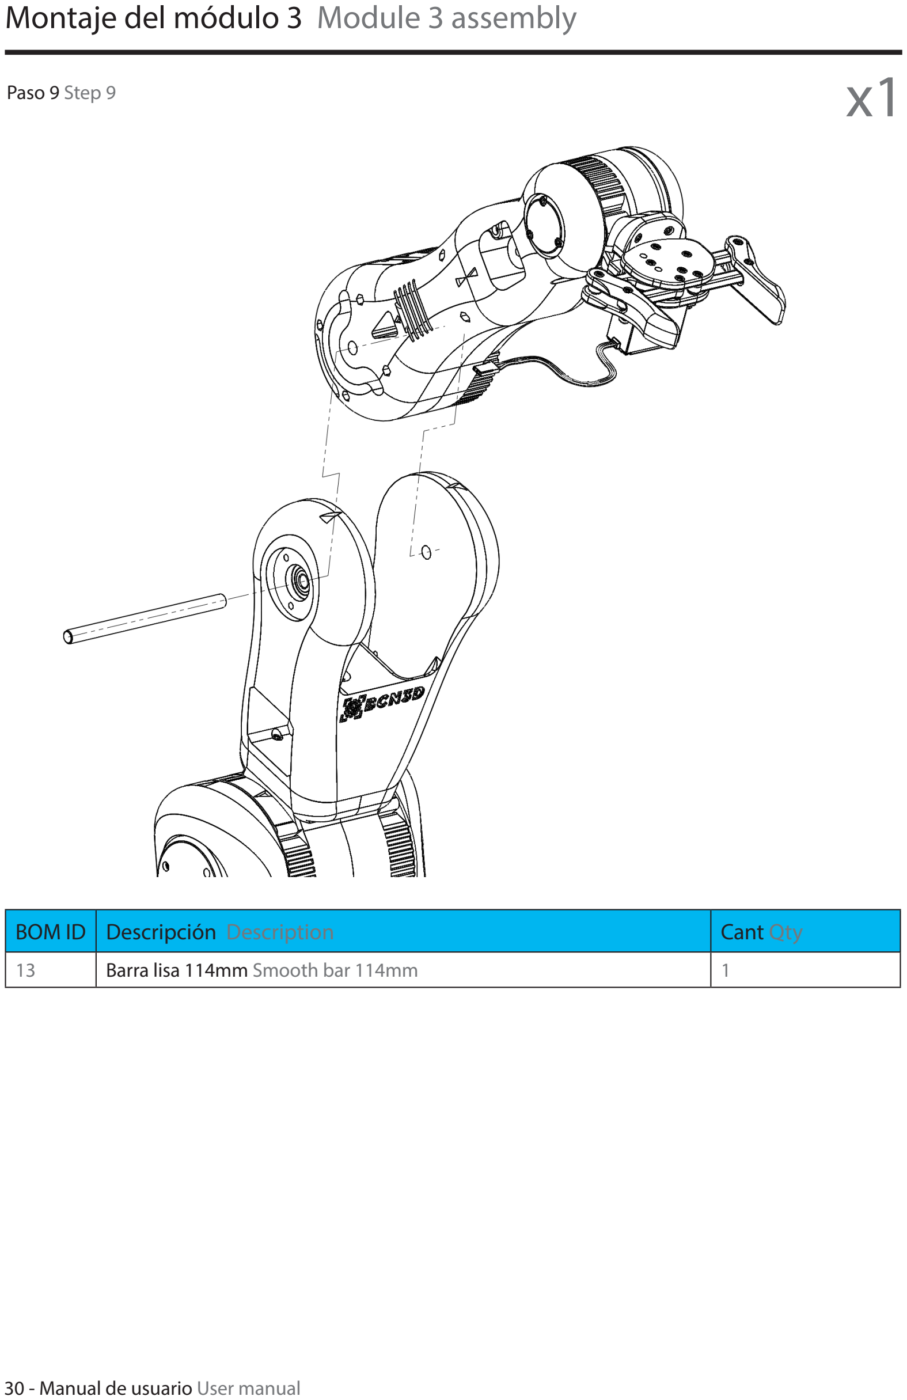
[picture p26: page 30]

BOM ID | Descripción Description | Cant Qty
13 | Barra lisa 114mm Smooth bar 114mm | 1
Paso 9 Step 9 | x1

## Montaje del módulo 3 Module 3 assembly

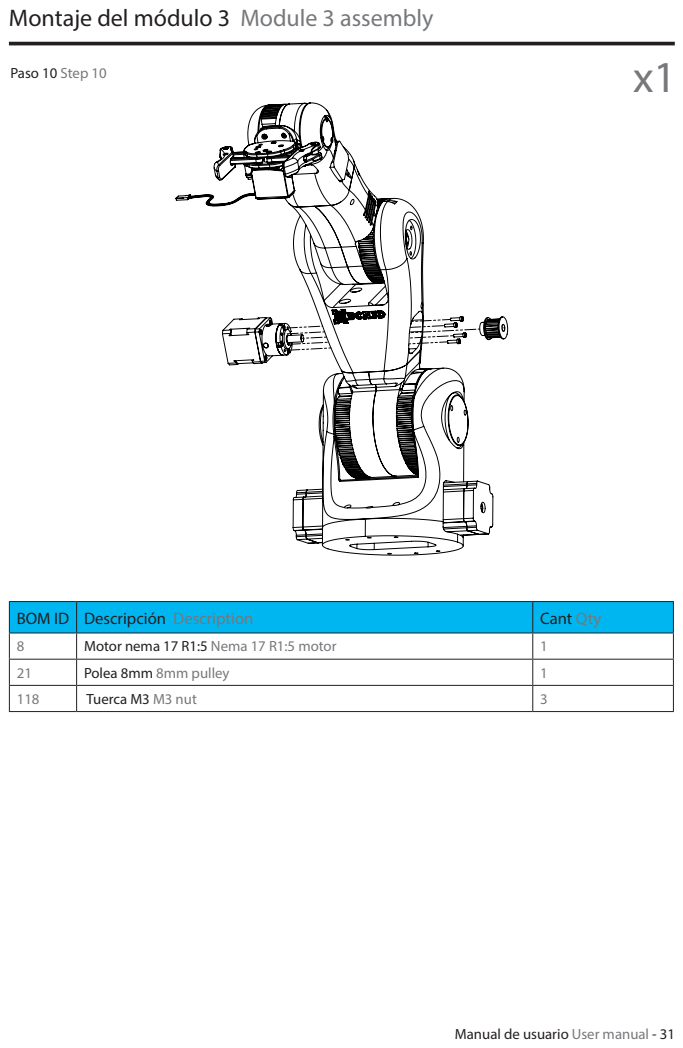
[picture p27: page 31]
Paso 10 Step 10

BOM ID | Descripción Description | Cant Qty
8 | Motor nema 17 R1:5 Nema 17 R1:5 motor | 1
21 | Polea 8mm 8mm pulley | 1
118 | Tuerca M3 M3 nut | 3

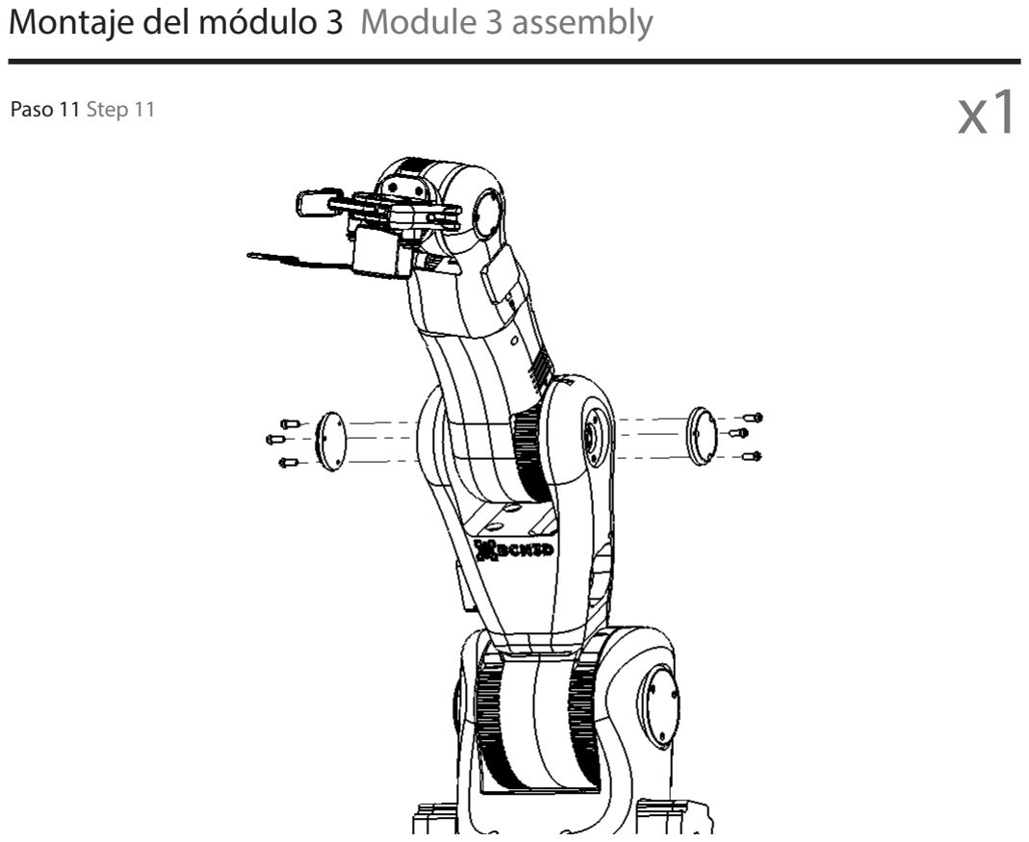
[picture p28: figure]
Montaje del módulo 3 Module 3 assembly; Paso 11 Step 11

BOM ID | Descripción Description | Cant Qty
230 | Pieza impresa tapa 3M1 Printed part tapa 3M1 | 2
101 | Tronillo M3 x 10mm M3 x 10mm srew | 1

## Montaje de la base Base assembly

BOM ID | Descripción Description | Cant Qty
- | Módulo 1M2 1M2 module | 1
32 | Base 550mm x 550mm 550mm x 550mm base | 1
111 | Tornillo M4 x 40mm M4 x 40mm screw | 4
120 | Tuerca autoblocante M4 M4 locknut | 2

## Montaje de la base Base assembly

BOM ID | Descripción Description | Cant Qty
- | Módulo 1M1 1M1 module | 1
112 | Tronillo M4 x 45mm M4 x 45mm srew | 6

## Montaje de la base Base assembly

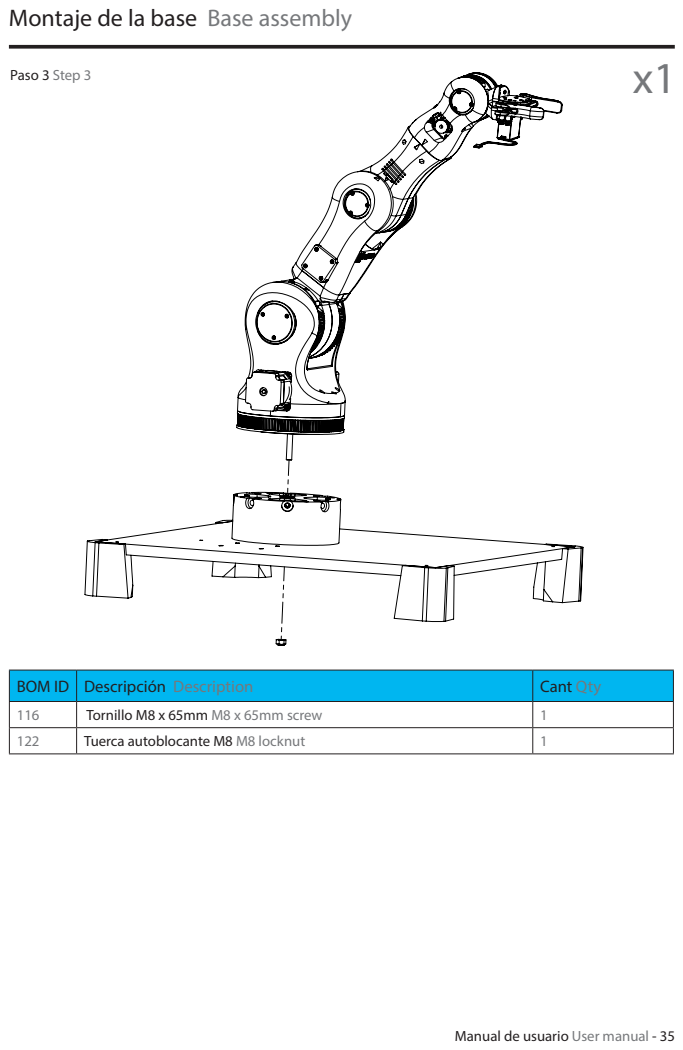
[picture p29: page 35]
Paso 3 Step 3

BOM ID | Descripción Description | Cant Qty
116 | Tornillo M8 x 65mm M8 x 65mm screw | 1
122 | Tuerca autoblocante M8 M8 locknut | 1

## Montaje de la base Base assembly

BOM ID | Descripción Description | Cant Qty
- | Módulo 1M3 1M3 module | 1
120 | Tuerca autoblocante M4 M4 locknut | 4
125 | Tornillo M4 x 30mm M4 x 30mm screw | 4

## Conexionado Connections

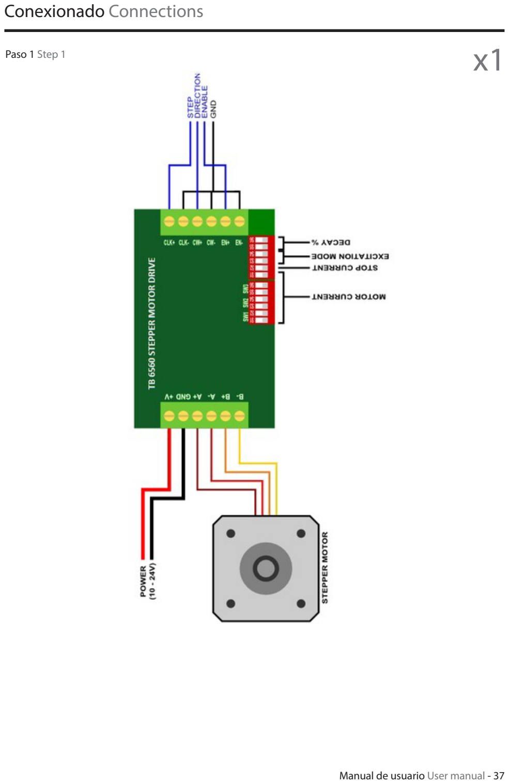
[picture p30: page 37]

Paso 1 Step 1 | x1

## Montaje de la base Base assembly

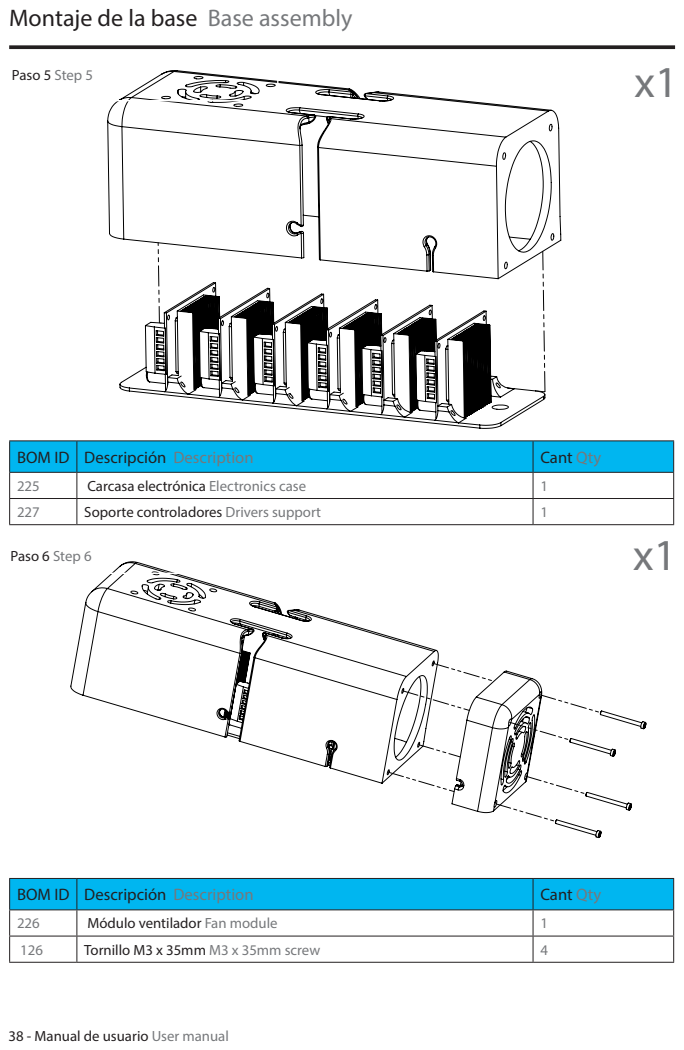
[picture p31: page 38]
Paso 5 Step 5; Paso 6 Step 6

BOM ID | Descripción Description | Cant Qty
225 | Carcasa electrónica Electronics case | 1
227 | Soporte controladores Drivers support | 1

226 | Módulo ventilador Fan module | 1
126 | Tornillo M3 x 35mm M3 x 35mm screw | 4

## Montaje de la base Base assembly

BOM ID | Descripción Description | Cant Qty
- | Módulo caja electrónica Electronics case module | 1
125 | Tornillo M4 x 30mm M4 x 30mm screw | 2

## Instalación del firmware Firmware installation

Arduino IDE

Arduino IDE es una plataforma que permite escribir código en un entorno limpio y ordenado. Una vez terminado podemos cargarlo en el arduino con solo pulsar un botón.
Estos són los passos a seguir para cargar el firmware. En nuestro caso, el firmware se llama “Marlin_BCN3D_Moveo” y está en una carpeta llamada Firmware.

Arduino IDE

Arduino IDE is a platform that allows you to write code in a clean and tidy environment. Once the code is written it, we can upload it to the arduino with just touching a button.
These are the steps to load the firmware. In our case, the firmware is called “Marlin_BCN3D_Moveo” and is located in a folder called Firmware.

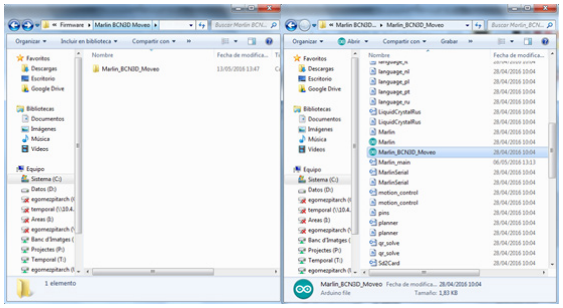
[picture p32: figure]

Una vez localizado el archivo “Marlin_BCN3D_Moveo.ino” hacer doble click en él para abrirlo. Cuando se haya cargado hacer click en herramientas y dirigirse a los apartados de “Placa”, “Procesador” y “Puerto”. Conectamos el Arduino en el PC. Abrimos el apartado de placa y seleccionamos nuestro modelo, Arduino Mega 2560.

Once you have located “Marlin_BCN3D_Moveo. ino” file, double-click on it to open it.
Click “Tools”, go to “Board”, and select Arduino Mega 2560.

## Instalación del firmware Firmware installation

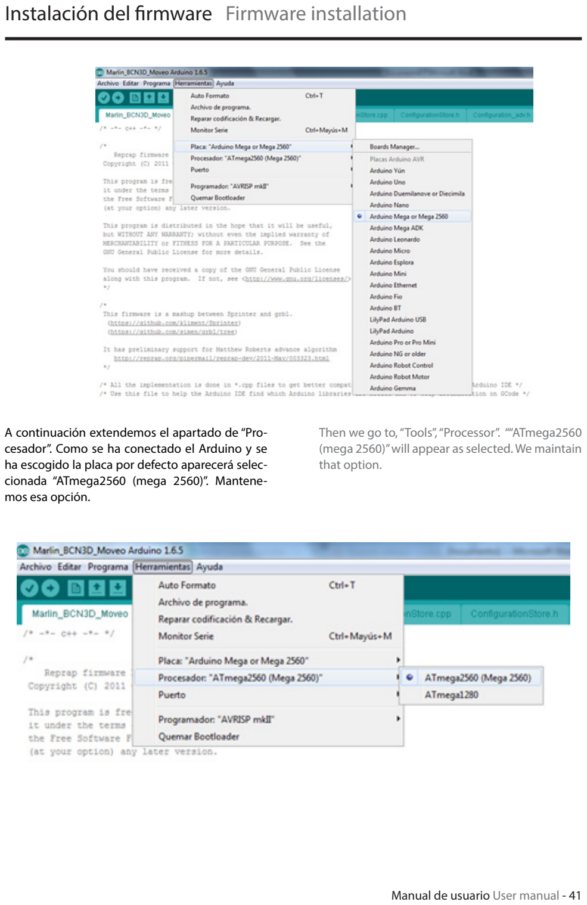
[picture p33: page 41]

A continuación extendemos el apartado de “Procesador”. Como se ha conectado el Arduino y se ha escogido la placa por defecto aparecerá seleccionada “ATmega2560 (mega 2560)”. Mantenemos esa opción.

Then we go to, “Tools”, “Processor”. ““ATmega2560 (mega 2560)” will appear as selected. We maintain that option.

## Instalación del firmware Firmware installation

El último parámetro es el del puerto. Hay que seleccionar el puerto que contenga el modelo de nuestra placa en el nombre, por ejemplo COM16 “Arduino Mega or Mega 2560”.

The last parameter is the “Tools”, “port”. You have to select the port that contains the model of your plaque in the name, eg COM16 “Arduino Mega or Mega 2560”.

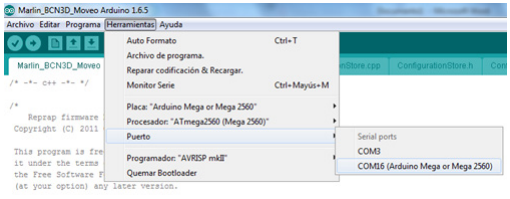
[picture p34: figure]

Para acabar hay que hacer click en botón de subir. Después de aproximadamente 1 minuto el firmware se habrá subido correctamente. Si hay problemas en la compilación descargar los drivers más actualizados desde la web de Arduino.

Finally, you must click the button “upload”. After about 1 minute firmware will be uploaded. If there are problems in the compilation, download the most current drivers from the website of Arduino.

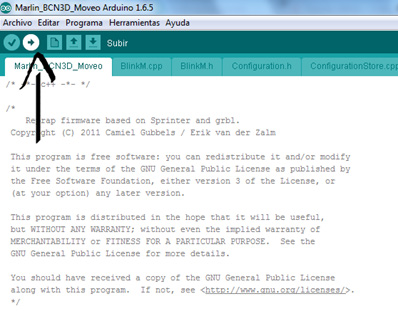
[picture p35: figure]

## ¿Cómo usar el BCN3D Moveo? How to use the BCN3D Moveo?

Pronterface

Pronterface es un programa destinado al testeo de impresoras 3D. Con él se pueden mover todos los ejes individualmente hacia todas las direcciones y también los extrusores. En la parte derecha hay un terminal de comandos con el que se pueden enviar líneas de gcode para mover los motores, leer las posiciones de cada motor y mover servo motores.
En nuestro caso, haremos uso del software Pronterface con el objetivo de mover el BCN3D Moveo. Para poder actuar sobre el BCN3D Moveo hay que establecer una comunicación entre Pronterface y el Arduino. Esto se consigue realizando los siguientes pasos. Primero se tiene que escoger el puerto COM en el que esté conectado el arduino.

Pronterface

Pronterface is a program for the testing of 3D printers. With it you can move all axes individually in all directions and also the extruders of your printer. On the right side of the program, there is a terminal command with which you can send gcode lines to move steppers, read the positions of each stepper and also move servo motors.
In our case, we will use the software Pronterface in order to move the BCN3D Moveo. To act on the BCN3D Moveo we must establish communication between Pronterface and Arduino. This is accomplished by performing the following steps.

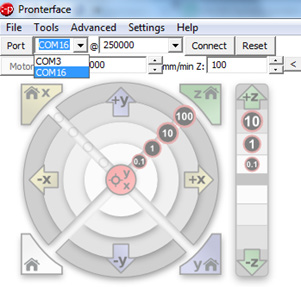
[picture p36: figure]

Atención: No se deben tener abiertos los dos programas (Pronterface y Arduino IDE) a la vez.

Please note that should not be open both programs (Pronterface and Arduino IDE) simultaneously.

## ¿Cómo usar el BCN3D Moveo? How to use the BCN3D Moveo?

El siguiente paso es escoger una velocidad de
250.000 baudios.

The next step is to choose a speed of 250,000 baud.

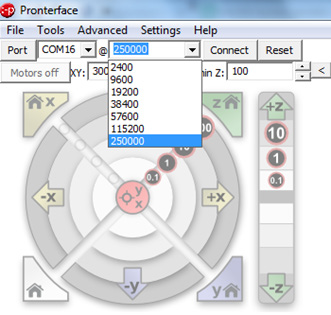
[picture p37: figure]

Finalmente para acabar de realizar la conexión hacer click en el botón “Connect”. Entre otras cosas aparecerá un texto notificando que nuestra impresora ya está online “Printer is now online”. A partir de ese momento se activará la función del terminal (situada en la parte inferior derecha) y la de mover los motores.
El círculo superior izquierdo nos muestra 3 de los 5 ejes (los principales). Con el movimiento de esos 3 ejes se pueden realizar aproximaciones y tests para encontrar las posiciones que más se adecúen a la secuencia de trabajo que se requiera. Una vez se hayan encontrado las posiciones el procedimiento es el de escribir un Gcode que contenga toda esa información.

Finally, to finish the connection, click the “Connect” button. Among other things, a text will appear notifying you that your printer is online “Printer is now online.”
From that moment, the function of the terminal (located on the bottom right) and the function of moving the motors will be activated.
The upper left circle shows 3 of the 5 axis (the main axis). With the movement of those 3 axes you can perform tests to find approaches and positions that are most suited to the sequence of work required. Once the positions have been found, the procedure is to write a .Gcode containing all this information.

## ¿Cómo usar el BCN3D Moveo? How to use the BCN3D Moveo?

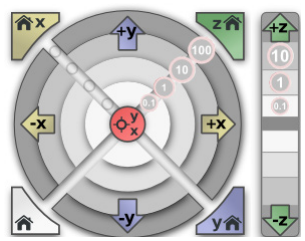
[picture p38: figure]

En éste círculo también se aprecian distintos valores, del 0.1 al 100. La unidad usada en los valores se refiere a un paso de los motores. Por norma general, cuando estamos testeando no se recomienda usar las opciones de 100 pasos.

In this circle also they appreciate different values, from 0.1 to 100. The unit used in the securities refers to a step of the engines. Generally, when we are testing, it is not recommended to use options 100 steps.

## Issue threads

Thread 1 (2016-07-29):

Is this derived from MANTIS?

i-make-robots, 2016-07-29:
https://hackaday.io/project/3800-3d-printable-robot-arm

miguelrochajr, 2016-08-02:
Looks like! But both seems to be great projects!

kitusmark, 2016-08-02:
Hi @i-make-robots !

Indeed, it's based on the awesome work by Andreas. It's not as advanced as his but we're working on it. Hope you like it and please help us improve it even more!

i-make-robots, 2016-08-02:
@kitusmark Please give Andreas credit in your github README and on your website.
I have acknowledged others for my Makelangelo robot.  I feel it's the least I owe them.

kitusmark, 2016-08-03:
@i-make-robots I'll update the README as soon as I can. Thanks!

jesper988, 2016-09-10:
1 month later.. Is not updated yet?

Closed 2016-10-10.

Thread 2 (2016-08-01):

Missing STL files: T2M1D, T2M1L, T3M1, and T4M

jakegaecke, 2016-08-01:
In the User Manual pdf, steps 4, 5 for Module 2 Assembly (page 11) step 2 for Module 3 Assembly (page 20), and step 2 for Module 4 assembly (page 22), all reference parts that don't seem to be published: T2M1D, T2M1L, T3M1, and T4M. These parts are also listed in the BOM. Can these parts be published?

jamesarm97, 2016-08-01:
I believe those parts are in the source files. I had the same problem but was able to generate them from the solid works files. I am attaching the ones generated from the CAD files. I guess someone can add them to the github as I haven't checked them out.

[Txx_Parts.zip](https://github.com/BCN3D/BCN3D-Moveo/files/394063/Txx_Parts.zip)

airshares, 2016-08-01:
I am looking for the .stl of those files as well

jamesarm97, 2016-08-01:
Check my previous comment. It should have a zip file attached with what I think are those files if someone can verify.

airshares, 2016-08-01:
Yep I see them now.  Thank you!  I did not look at that file earlier.

kitusmark, 2016-08-02:
@jamesarm97 if you could make a pull request it would be awesome as you have already generated the files.

jamesarm97, 2016-08-02:
I did the Pull request, someone will need to confirm and close it.

jakegaecke, 2016-08-04:
Exactly what I needed. Thank you!

Closed 2016-08-04.

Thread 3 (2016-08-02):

Could someone please provide more accurate information on the motors

IAmOrion, 2016-08-02:
Could someone please provide more accurate information on the motors, I'm trying to source parts in the UK, and the motors listed in the BOM are too generic.  The only 1 with enough info was the Nema 14 36mm SM35HT36 > that I can find, but not a clue on any of the others.

miguelrochajr, 2016-08-02:
I was able to find all the parts at www.aliexpress.com typing the specifications given on the Bill Of Materials. Some of the Nema's have some little differences such as the protruding connection at the sides like [this one](http://www.aliexpress.com/item/Nema-17-Stepper-Motor-bipolar-4-leads-34mm-12V-0-4A-26Ncm-36-8oz-in-3D/32376850840.html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,searchweb201602_2_10057_10056_10055_10037_10049_301_10059_10033_10058_10032_10017_405_404_10060_10061_10062_412,searchweb201603_6&btsid=ad284de6-6f86-483b-85b6-3c3575afee5e). For the rest, I just looked at thee Datasheet.

IAmOrion, 2016-08-02:
Thanks miguelrochajr, that's good to know, I'll take a look at AliExpress now.

Have you completed your build?  If you get a chance could you paste links for the motors from your order history?

Kind regards

marcovanschagen, 2016-08-07:
Same question, and I will purchase trough ebay.

marcgenevat, 2016-08-07:
Have you estimated the approximated costs of the hardware?  I'm the CEO of a edtech company and I can't wait to see how my students react with this awesome project. Thank you guys!

kitusmark, 2016-10-03:
Hi people!

Take a look at the updated BOM file as we have added some extra info and corrected other.
https://github.com/BCN3D/BCN3D-Moveo/commit/0866a92501277636f76000a195d8a16d44b5b476
Thanks for the feedback!

@marcgenevat the cost of hardware is arround 300-400€ depending on where you buy the parts. Everything is pretty standard and you'll be able to source equivalent parts.

AlexanderZhang11, 2016-10-10:
hi IAmOrion ,have you finished your work? Do you know how to connect wiring diagram?

helgrind, 2017-07-04:
I just bought these. Missing the first motor though as I hear that one is a contentious choice so we'll buy it later I think. Prices are in pounds sterling.

BOM ID  Price   Link

8            23.14  https://www.aliexpress.com/item/Best-Price-Extruder-Gear-Stepper-Motor-Ratio-5-1-Planetary-Gearbox-Nema-17-Step-Motor-OSM/32801086766.html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

9            62.61  https://www.aliexpress.com/item/P-romotion-1-PC-Stepper-Motor-Nema23-425oz-in-112mm-3A-23HS9430-CNC-kit/32820939354.html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

11          5.97    https://www.aliexpress.com/item/Free-shipping-and-Quality-17HS3401-4-lead-Nema-17-Stepper-Motor-42-motor-42BYGH-1-3A/32723884250.html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

3            34.51  https://www.aliexpress.com/item/TB6600-stepper-motor-Driver-Controller-4A-9-42V-TTL-16-Micro-Step-CNC-1-Axis-NEW/32629936087.html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

10          14.03  https://www.aliexpress.com/item/1-8degree-35mm-1-4Kg-cm-1A-2phase-hybrid-stepper-motor-NEMA14-Robot-Motor-35HY34-1004/32576815079.html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

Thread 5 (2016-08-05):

"T" parts are missing

laovorak, 2016-08-05:
There is no T2M1D, T2M1I, T3M1, T4M1 in the STL section.

jamesarm97, 2016-08-05:
This was already discusses. Not sure why when I look at my pull request it shows 0 additions and 0 deletions yet it has files attached. Has someone committed/ approved the pullnrequest yet?

https://github.com/BCN3D/BCN3D-Moveo/pull/4/files

kitusmark, 2016-08-05:
@laovorak Merged! Sync your repos and the parts should show up.
Thanks @jamesarm97 :+1:

Closed 2016-08-05.

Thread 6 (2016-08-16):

Wiring Diamgram is missed

ildarjaleh, 2016-08-16:
Please add wiring diagram to the instruction.

AlexanderZhang11, 2016-10-10:
Yes, I am also puzzled by the wiring diagram problem. I really hope it can be updated as soon as possible.

Mocsany, 2016-10-13:
Yes, please provide wiring diagram!

knoxxr, 2017-09-09:
Need wiring diagram too.
I have ask about power supply.
Moveo use 24v power supply in BOM and use voltage converter 24v to 12v.
Why use 24v power instead 12v power.
Ramps 1.4 normaly use 12v power supply.
Is passible 12V, 320W power supply directly?

xy23, 2018-08-31:
Hello I am close to finish the printing part of Moveo and I will start the wiring process in the next few Days.
My Question is, is ther now any wiring Diagramm here on Github or can someon give me some hint where I can find one?

fc-lapac, 2019-11-05:
Any news on that?

michelgokan, 2021-07-03:
Where is the wiring diagram?

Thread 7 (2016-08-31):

Detailed BOM

Warcorer, 2016-08-31:
Hello,

The Bill of Materials isn't very detailed on specifications of parts. Could the list please be updated? Issues such as Power Supply 24V a 12V? Is that supposed to mean 24V DC converter to 12V DC? Also stepper nema 17 R 1:5? Is this supposed to mean a Nema 17 Stepper Motor with 5:1 planetary gearbox? Please review the BOM and update the details so it is easier for other people to make this open source project from BCN3D.

Thanks,

Michael

Lostinthe907, 2016-09-29:
I Am having the same Problems I cannot seem to find the Right parts based on the Description of BOM. common part numbers of users who already built it would be Awesome. I don't know much about this stuff But I want to Learn the most I can. e.g. Belt Numbers, common motor numbers, and maybe places to buy the parts. I am in the US so any help would be Really Grateful!!!!

ShopMonkey, 2016-09-30:
For the belts I went to [PolyBelt](http://shop.polybelt.com/main.sc)

Specifically Here are the:
[The Belting ](http://shop.polybelt.com/16T5-Open-End-Belt-Roll-Polyurethane-with-Steel-Cords-B16T5-MPS.htm)
[The 10 tooth Pulley ](http://shop.polybelt.com/27T5-10-2-Aluminum-10-Tooth-Pulley-1505mm-OD-P27T5-10-2A.htm)
[The 14 tooth Pulley](http://shop.polybelt.com/27T5-14-2-Aluminum-14-Tooth-Pulley-2145mm-OD-P27T5-14-2A.htm)

Keep in mind that these pulleys are not predrilled. Witch lets you match to the steppers if you cant find exactly 8mm shafts. You can drill and ream them on a drill press. Use a good reamer.

Stepper motors I got on ebay.

All the fasteners I got at [McMaster-Carr](http://www.mcmaster.com/#)

The joint axles I got ebay

The rest is easily available .

Open builds has power supplies and other bits.

Lostinthe907, 2016-09-30:
Cool. Thanks! @ShopMonkey

kitusmark, 2016-10-03:
Check out the new BOM file
https://github.com/BCN3D/BCN3D-Moveo/commit/0866a92501277636f76000a195d8a16d44b5b476
Thanks for the feedback!

volo63, 2016-11-25:
Hi,
got the same problem.
I´m located in Germany and I want to start this project for education.
It will take me a lot of time to "redesign" the project because I´m missing the technical details for some BOM parts.
Is there anyone who did or is doing the project in Europe.
My prefered supplier is Conrad electronic and Reichelt electronic.

Is there anybody out there? :))

Volker

AnykeyNL, 2016-11-25:
HI,

I am based in netherlands and building one. I have almost everything
printed out and sourced all components ( I hope). Starting the assembly
next week probably :-)

Regards,
Richard

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

avanrijswijck, 2016-12-19:
We are building the moveo @ the kaasfabriek. Education will be the main purpose. When ready and tested we will use it for school projects. We will provide all the parts and start an educational programm for primary schools and high schools.

volo63, 2016-12-19:
Hi, we will also build up the moveo robot arm. Would be nice to work together in a virtuell team. We will use it for our Volkswagen Campus Digital in Hannover to train students.

dutchrazor, 2017-01-01:
Here are some links I found for the most matching stepper motors. (the 34mm NEMA 17 is a 0.9* version, 1.8* was sold out)

STEPPER NEMA 17 60mm  (SM42HT47-1684 1,8o step, 1,6 A, 3600 g·cm)	1	N	Y		http://eu.stepperonline.com/nema-17-60ncm85ozin-064a-bipolar-stepper-motor-17hs240644s-p-19.html

Power Supply 24V 320W	1		Y		http://eu.stepperonline.com/switching-power-supply-350w-24v-146a-for-cnc-router-kits-115v230v-s35024-p-177.html
SERVO MOTOR 180§ 55G TORQUE=13KG/CM	1		Y		http://www.tinytronics.nl/shop/Futaba-S3003-Servo
Stepper nema 17 R 1:5 (17HS19-1684S-PG5 ( step 0,35o , 2Nm, 1,68A))	1	N	Y		http://eu.stepperonline.com/gear-ratio-51-planetary-gearbox-high-torque-nema-17-stepper-17hs191684spg5-p-40.html
Nema 23, 112mm, Ø8mm flat shaft (SM57HT112-3004A step 1,8o 3A 28Kg·cm)	2	N	Y		http://eu.stepperonline.com/high-torque-nema-23-cnc-stepper-motor-113mm-3nm425ozin-23hs454204s-p-127.html
 Nema 14 36mm (SM35HT36-1004A, 1,8o step, 1A, 1400g·cm)	1	N	Y		http://eu.stepperonline.com/nema-14-bipolar-stepper-54v-08a-18ncm255ozin-14hs130804s-p-93.html
Nema 17 34mm (SM42HT33-1334, 1,8o step, 1,33A, 2200 g·cm)	1	Y	Y		http://eu.stepperonline.com/nema-17-stepper-motor-34mm-12v-04a-26ncm37ozin-17hs130404s-p-166.html

bullestock, 2017-03-20:
I have to join the chorus here: The current BOM is a bit of a joke.

First, why on earth have you chosen to make a PDF of a screen dump of an Excel sheet?! Come on, guys! Open the Excel sheet in LibreOffice, then export it to an open format!

Secondly, specifications such as "Chrome steel smooth bar-134 mm" are pretty useless. How can I know which diameter is required?

chexov, 2017-03-20:
You guys know you can make pull request and fix it instead of complaining right? This is how OSS works pretty much.

bullestock, 2017-03-20:
@chexov How can I do that when a) no source exists for the BOM b) I have no idea what the specifications are for those "smooth steel bars"?

bullestock, 2017-03-21:
@AnykeyNL do you have any details on items such as steel bars etc?

bullestock, 2017-03-21:
Digging around in the forum, it turns out that the steel bars should be 8 mm.

volo63, 2017-03-21:
Hi Torsten,

we already worked our own BOM.

I don´t have any experience with github.

If you are interested in our BOM I could send it.

We also made the first  -bad - expieriences with the cheap motor drivers.

Also we have some not solved issiues.

What is your robot arm status?

greetings

volker

Gesendet: Dienstag, 21. März 2017 um 13:04 Uhr
Von: "Torsten Martinsen" <notifications@github.com>
An: BCN3D/BCN3D-Moveo <BCN3D-Moveo@noreply.github.com>
Cc: volo63 <vloebe@web.de>, Comment <comment@noreply.github.com>
Betreff: Re: [BCN3D/BCN3D-Moveo] Detailed BOM (#7)

Digging around in the forum, it turns out that the steel bars should be 8 mm.

—
You are receiving this because you commented.
Reply to this email directly, view it on GitHub, or mute the thread.

volo63, 2017-03-21:
one more:)

our cylinders are made from us.

if you need I could ask in the workshop to produce more.

Do you need the cylinders?

Gesendet: Dienstag, 21. März 2017 um 13:04 Uhr
Von: "Torsten Martinsen" <notifications@github.com>
An: BCN3D/BCN3D-Moveo <BCN3D-Moveo@noreply.github.com>
Cc: volo63 <vloebe@web.de>, Comment <comment@noreply.github.com>
Betreff: Re: [BCN3D/BCN3D-Moveo] Detailed BOM (#7)

Digging around in the forum, it turns out that the steel bars should be 8 mm.

—
You are receiving this because you commented.
Reply to this email directly, view it on GitHub, or mute the thread.

bullestock, 2017-03-22:
@volo63 I found a BOM in Excel format in the forum, but I would like to see yours too. I plan to produce an improved BOM and upload it to github. (I have not yet started on my arm, I am just doing research ATM).

I am not sure I understand what you mean by "cylinders"?

anyrules, 2017-03-23:
Hello All,

I have started to print out the components and meantime I looking for components and Fasteners.
Unfortunately it's really do not easy to recognize all components based on the PDF.
(Some of them withdrawned from the market)
First we need to print out after we can concluded for the  parts.
If somebody have a fresh detailed BOM and send to me I really appreciate it.
Thanks in advance,
Regards
  Istvan
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
anyrules, 2017-03-27:
Hi Volker,

did you got my mail?
Regards,
  Istvan

bullestock, 2017-03-27:
@anyrules can you please send to me too, at torsten@bullestock.net - thanks

modulab, 2017-03-27:
Hey guys! Can't you just upload it on a drive somewhere and share the link?
Thanks

Warcorer, 2017-03-28:
Could I have it emailed as well

Mjjagosz@gmail.com

Thanks,

Michael J Jagosz

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

volo63, 2017-03-29:
Hi,

please send me your email, than I will send my BOM

greetings

volker

Gesendet: Mittwoch, 22. März 2017 um 11:14 Uhr
Von: "Torsten Martinsen" <notifications@github.com>
An: BCN3D/BCN3D-Moveo <BCN3D-Moveo@noreply.github.com>
Cc: volo63 <vloebe@web.de>, Mention <mention@noreply.github.com>
Betreff: Re: [BCN3D/BCN3D-Moveo] Detailed BOM (#7)

@volo63 I found a BOM in Excel format in the forum, but I would like to see yours too. I plan to produce an improved BOM and upload it to github. (I have not yet started on my arm, I am just doing research ATM).

I am not sure I understand what you mean by "cylinders"?

—
You are receiving this because you were mentioned.
Reply to this email directly, view it on GitHub, or mute the thread.

CaptainMack, 2017-05-02:
If you could send the BOM to c.laursen@montem.io I would be grateful!

helgrind, 2017-07-04:
Does anyone have more information about the M4 and M3 brass inserts? Are there recommended lengths etc? Also, are the spacers aluminium ones? Ta

Aerrios, 2017-08-10:
Hi,
can you please send me your detailed BOM to travnicek@allcomp.cz

Thank you very much!

helgrind, 2017-08-10:
Can we get the detailed BoM in a forked repository or something publicly available online? It seems bad practice to turn this issue thread into an email request page...

tejas4patel, 2017-08-10:
Thank you @helgrind, totally agree..

dylandesouclin, 2018-01-14:
Bonjour,
c'est vrai que cette BOM est très compliquée à détailler, je voudrais si possible une BOM plus détaillée
Merci

joealthaus, 2018-01-18:
https://github.com/BradyHooverDesigns/BCN3D-MOVEO-BOM

russelbradley, 2018-09-04:
I'm confused for the smooth rods.
BOM tells me to get lengths of 42mm, 80mm, 114mm and 134mm. While the solidworks file says 50mm, 80mm, 121mm and 140mm respectively. Which one should I get?

Thanks in advance

mcprakash, 2018-10-09:
Also for the chrome steel smooth bar, what is the sectional dimension ? M8?

russelbradley, 2018-10-09:
> Also for the chrome steel smooth bar, what is the sectional dimension ? M8?

Yes 8 mm diameter.

mcprakash, 2018-10-11:
Just a quick question. We are using a 24V to 12V power converter and a 24V power supply. Any reason why we are not using a 12V power supply directly. Also, which components work on 24V and which on 12 V ? Thanks again.

mcprakash, 2018-10-28:
Had another quick question. Which material would be great for 3D Printing the outer body for long lasting (due to regular wear and tear) and stability of the arm

TacticalPanda028, 2019-04-27:
> @russelbradley还有另一个快速的问题。哪种材料可以很好地进行3D打印，使外部机身持久（由于经常磨损）和手臂的稳定性

Recently I have just started this project, I do not know if your project has been successful? This response may not be timely, and I can tell you that I am using components printed on PLA materials

russelbradley, 2019-04-27:
> @russelbradley Had another quick question. Which material would be great for 3D Printing the outer body for long lasting (due to regular wear and tear) and stability of the arm

I used PETG filaments from esun.

mcprakash, 2019-04-27:
@russelbradley I tried ABS. It is just a mess printing with ABS due to several reasons. There are still a few parts I need to print and then finally assemble them. An assemble video would be great to start, but if you are also building it, it would be great to stay connected and build together.

fc-lapac, 2019-11-05:
The BOM uses a power supply of 24v 15A, and a converter from 24v to 12v, usually people use with 10A. So could I just use a power supply of 12v 30A from head start and forget about the converter? will I use the 24v for anything? I haven't found a good electronics diagram that explain why should i have the 24v

jrgilman, 2021-03-19:
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

Did you ever figure out the right lengths? Also, the BOM doesn't list a 42mm anymore, and looking at the instructions I can't see one being used anywhere. What was this used for in the past?

johnmbiker, 2022-12-01:
I have printed the parts but not ordered the electronics and bolts yet.  After looking around much, I found this guy's detailed BOM on instructables with links.  I can't vouch for it yet but hope this helps someone.  Look for the google docs spreadsheet download.
https://www.instructables.com/Build-a-Giant-3D-Printed-Robot-Arm/

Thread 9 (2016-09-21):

Igus rails in BoM -- are these needed?

dtmille2, 2016-09-21:
The following parts are listed in the BoM's but not shown in the instruction manual or the CAD assembly:

LINEAL GUIDES IGUS-WSQ_06-134mm
LINEAL GUIDES IGUS-WSQ_06-114mm
LINEAL GUIDES IGUS-WSQ_06-080mm

Am I missing something or are these not needed?

Thanks!!

ShopMonkey, 2016-09-21:
I'm using regular 8mm rod (shafting) I don't see the need for lineal guides. They are in fact joint axles. Don't skimp on the bearings. I bought some cheep ones and they are unusable.

kitusmark, 2016-10-03:
Hi @dtmille2 and @ShopMonkey

We've updated the BOM file. Please take a look and get back to me.

https://github.com/BCN3D/BCN3D-Moveo/commit/0866a92501277636f76000a195d8a16d44b5b476

Thanks for the feedback!

dtmille2, 2016-10-23:
Thanks for updating the BoM, the additional stepper motor part numbers are great.

Unfortunately items 12, 13, and 14 are still not fully defined -- what diameter should the bars be?  6mm?

Closed 2016-11-20.

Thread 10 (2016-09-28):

Lineas Guides

BigSus, 2016-09-28:
Estamos preparando lo necesario para montar un brazo Moveo y según el BOM las barras lisas que usáis son de Igus. Concretamente las referenciais como  IGUS-WSQ_06, pero dicha referencia por lo que veo se corresponde con guías (http://www.igus.es/Search?q=WSQ-06), no con varillas. ¿Podéis especificar un poco más que tipo de varillas usáis y su diámetro?

Gracias

kitusmark, 2016-10-03:
Hola @BigSus.

Hemos actualizado el BOM. Échale un ojo a ver si hemos resuelto tus dudas.

https://github.com/BCN3D/BCN3D-Moveo/commit/0866a92501277636f76000a195d8a16d44b5b476

Gracias por el feedback

BigSus, 2016-10-03:
¿Faltaría indicar que las barras son de 8 mm no?

dtmille2, 2016-10-23:
Yes what diameter are the bars meant to be?

dtmille2, 2016-10-23:
Just pulled up the SolidWorks assembly file and from the name of the shaft parts it looks like they are meant to 8 mm diameter--please update the BoM, thanks!

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

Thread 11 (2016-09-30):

CAD files don't assemble in Fusion 360

Mocsany, 2016-09-30:
Hello, everyone I am having a hard time to put all the files into one assembly in Fusion 360. Is there anybody out there who has managed to do it? I am new to Fusion 360 and CAD in general so I may be not doing it right. No matter how I upload the files they don't assemble into one whole piece as I would like them to be.

macinblack, 2017-02-02:
It's a Solidworks design...

majoon, 2017-02-02:
There is absolutely no problem with the assembly in fusion 360 as long as all the files are uploaded together and the correct file is selected as the main assembly (there are many sw assemblies in the folder.)

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

spad, 2018-03-28:
Upload all solidworks files and select "BCN3D Moveo assembly" as top level assembly. It works for me.

soswow, 2018-04-18:
There are still some problems after importing and choosing "BCN3D Moveo assembly" as a main assembly.
1) All the bolts and blue caps are out of components where the suppose to be, and after enabling history copy-pasting them into appropriate component causes their move out of place
2) There are some empty components with name "Sistema rodaments". Also there is a error document generated.

Henke1983, 2020-02-29:
Here is complete assembly.
https://github.com/magnuspyke/BCN3D-Moveo/tree/master/CAD

I think this issue can be closed.

soswow, 2020-02-29:
Great! thank you! I can't close it, but it can be.

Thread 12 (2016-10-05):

Any advise on printing these large components

AnykeyNL, 2016-10-05:
Hi, I just bought a sigma to print these things. Is there any advise on printer settings for especially these large components? Like layer height, infill and material choice?

Regards,
Richard

kitusmark, 2016-10-06:
Hi @AnykeyNL !

Hope you like our Robotic Arm design and the BCN3D Sigma. I think it's better to open a post on the forum as you will be getting more feedback than here.

https://www.bcn3dtechnologies.com/es/forums/

Thanks and have fun!

AnykeyNL, 2016-10-06:
Thanks, I guess I was blind yesterday as I did look at the forum, but did not see a Moveo section.

Closed 2016-10-06.

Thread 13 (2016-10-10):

Do we should pay for the wiring diagram?

AlexanderZhang11, 2016-10-10:
I cannot find the wiring diagram in the resource list. I am puzzled by the problem of wiring. So does it mean we should pay for this diagram?

MarcusWolschon, 2016-12-15:
Is this a duplicate of
Wiring Diamgram is missed #6
?

kitusmark, 2017-02-02:
Duplicate on #6

MohammedAhamed, 2017-06-11:
I run the project  as graduation project  with some modifications   if any one want help   connect to me  for free  by email  mo.ah.has2014@gmail.com

Closed 2017-02-02.

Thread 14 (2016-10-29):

A new software to control moveo

darenwai, 2016-10-29:
Finally a software and firmware to control the zortrax or moveo robotic arm.
14days trial. US25 per software. Please support me. Thanks.

Demo: https://youtu.be/wO6RP1ZqzVk

Features:
-Can control two arduino mega with ramps1.4. A total of 12axis.
-12axis can be played in a single gcode file.
-Why 12 axis? Normally a 6axis robotic arm is not sufficient to solve real world problem.
 So, the extended axis are used to assist the robotic arm to perform task.
-Use joystick to control.
-Support two types of gripper. Magnetic and servo.
-Auto recording of gcode.
-Can play line by line of gcode and delete a single line of gcode.
-Can save and playback unlimited gcode file.

Download the software and firmware at https://drive.google.com/file/d/0BzSicdTSN7f9V25XYm5UdkxEMzg/view?usp=sharing
Email: testdebug@hotmail.com

Hassan3ysaaopp, 2023-06-07:
How can i buy this software ?

darenwai, 2023-06-08:
To get the license code for basic edition without computer vision feature:

1.https://www.paypal.com
2.After login
3. click on Tool/Send money
4. Click on Pay for goods or services.
5 Type ***@***.***
6. Click next. You should see Quantum Software
7. Put USD 35
8. On Note. You can put your device ID number on the software registration page.
9. I will send you the serial number to register. Thank you.

Sent from Mail<https://go.microsoft.com/fwlink/?LinkId=550986> for Windows

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

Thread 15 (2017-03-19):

Moveo D-H Parameters

MarcoAntonini, 2017-03-19:
Moveo is awesome project! Thanks for sharing it!
I finished assembly my Moveo, I would like to drive it with a direct and inverse kinematics.
Someone has already calculated the d-h parameters (Denavit–Hartenberg) of this robot?

MarcoAntonini, 2017-03-27:
Ok, calculated it .
Added a joint-6 to expand sixth dof rotary .

Moveo D-H Parameters (5/6DOF)

MarcoAntonini, 2017-03-27:
Ok, calculated it .
Added a joint-6 to expand sixth rotary dof.

**Moveo D-H Parameters (5/6DOF)**

```
#            L2
#   j2  *----------*   j3
#       |       L3 |
#   L1  |          *   j4
#       |       L4 |
#   j1  *          *   j5
#               L5 |
#                  *   j6
#                 | |
```

joint | Alpha | A | D
-----|-------|--|--|
1 | 0 | 0 | L1
2 | 90 | 0 | 0
3 | 0 | L2 | 0
4 | 90 | 0 | L3
5 | -90 | 0 | 0
6 | 90 | 0 | L4

kitusmark, 2017-03-30:
Wow @MarcoAntonini !

Awesome job. I would be very interested if you share how you control your Moveo. Is it ROS or something? That looks pretty neat

MarcoAntonini, 2017-03-30:
Yes, LinuxCNC has realtime kernel !
Certainly I will share documentation as soon as possible
I'm studying for stepper signals generation, for now just a simulation but very impressive :

https://www.youtube.com/watch?v=55SpbKL9n8U

kitusmark, 2017-03-30:
That's really impressive. Didn't know about linuxCNC (used Mach3 instead). It seems like a very configurable software as you can render the full robot in 3D.
Is there a way of generating the trajectories within the software? or any way of make the robot learn the movements?
truly impressive

MarcoAntonini, 2017-03-30:
LinuxCNC is similar to Mach3,It has a python scripting language to create your own robot/machine.
It generate the trajectories in non-linear movements from XYZABC cartesian coordinates using direct kinematics.
For current configuration (5 joint) only X-Y-Z-A-B are supported. Add sixth joint for C Axes.

This simulation using the A,B axis , rotate a effector around a fixed point : https://www.youtube.com/watch?v=SHPSGXtctZM ,seems to properly work :)

pkmcnc, 2017-03-30:
@MarcoAntonini this is great! How did you make a visualisation?

MarcoAntonini, 2017-03-30:
@pkmcnc , use the linuxcnc vismach http://linuxcnc.org/docs/html/gui/vismach.html

abdelaziz94, 2017-05-28:
hello sir did you calculate the inverse kinematics of this robotic arm  ?
if you did it can you provide it to me please ?

tsibos22, 2018-01-06:
Hallo everyone.
Has anyone the inverse kinematics of moveo in excel?
Thanks

tegri, 2018-11-28:
Any news on this one guys? I have found some inverse kinematic solutions on the Internet. Thought you guys might be interested. Here is link: http://www.chew-z.it/wiki/doku.php?id=moveo:moveo_kinematic

Thing is it is not in English.

EBMare, 2021-04-19:
@MarcoAntonini do you have the DH-parameters now? Cuz I need them too

EBMare, 2021-04-20:
https://stackoverflow.com/questions/67159164/denavit-hartenberg-6dof-moveo-inverse-kinematic-robot-arm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

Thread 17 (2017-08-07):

URDF for moveo

jesseweisberg, 2017-08-07:
Has anyone created a URDF file for the moveo for use in physics simulators?

It seems to be a pretty simple process with access to Solidworks, but a long and daunting one to construct such a complex URDF file from STL files.  Unfortunately, I don't have access to Solidworks– if anyone one has Solidworks and can do this, it would save others (myself included) a lot of time and give people the tools to do awesome things in simulation with the moveo!

jesseweisberg, 2017-11-28:
URDF can be found here: https://github.com/jesseweisberg/moveo_ros

Closed 2017-11-28.

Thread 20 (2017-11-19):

Error compiling firmware

HedronUser, 2017-11-19:
I'm getting this error with Arduino 1.8.5

>

sketch\Marlin_main.cpp:2666:36: warning: invalid suffix on literal; C++11 requires a space between literal and string macro [-Wliteral-suffix]

         LCD_MESSAGEPGM(MACHINE_NAME" "MSG_OFF".");

                                    ^

In file included from sketch\SdFile.h:27:0,

                 from sketch\cardreader.h:8,

                 from sketch\Marlin_main.cpp:44:

SdBaseFile.h:38: error: using typedef-name 'fpos_t' after 'struct'

 struct fpos_t {

        ^

In file included from sketch\Marlin.h:10:0,

                 from sketch\Marlin_main.cpp:30:

c:\users\dave\appdata\local\arduino15\packages\arduino\tools\avr-gcc\4.9.2-atmel3.5.4-arduino2\avr\include\stdio.h:950:33: note: 'fpos_t' has a previous declaration here

 __extension__ typedef long long fpos_t;

                                 ^

exit status 1
using typedef-name 'fpos_t' after 'struct'

>

HedronUser, 2017-11-19:
Can I just change the reference name since it seems to have an overlap with existing internal stdio.h code...?

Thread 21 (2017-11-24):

Can now use Moveo with ROS and Moveit

jesseweisberg, 2017-11-24:
I've been working to control the Moveo with ROS both in simulation and the real, physical robot-- so far I've gotten some nice functionality working and wanted to share with everyone.  So far, the following functionality works and you can grab all my work thus far from this repo here, and get it working for yourself:
https://github.com/jesseweisberg/moveo_ros

1) Simulate motion planning for the Moveo in RVIZ using Moveit (i.e. plan and execute trajectories)
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

2) Read current pose & position of the simulated Moveo end-effector in 3D coordinate space.  You can also plan & execute a trajectory by inputting a 3D coordinate and pose for the end-effector.

3) Execute these trajectories on the real robot (using an Arduino MEGA 2560, RAMPS 1.4) so that they match the movement in simulation.

4) There is a ton more to do using ROS to allow the Moveo to do incredible things.  I'm currently working on integrating closed-loop control with additional sensors, along with implementing vision feedback to make the control more robust and see how far we can take the Moveo!  If anyone wants to contribute or has any ideas for the future of this project, please let me know!

**I'll have a video of all this stuff up and working in the next couple of days

I tried to detail all the steps to get it running on my github repo, but probably missed some, so please let me know if you have trouble getting it up and running.  Tested on Ubuntu 16.04, and you may have to make slight modifications if running something else-- but definitely worth it.

-Jesse

alequeiroz, 2017-12-09:
Hello @jesseweisberg i'm very interested in visual recognition with moveo, do you already have a repo that we can contribute?

jesseweisberg, 2017-12-11:
Hi Alessandro, I'll actually have something up either tomorrow or Tuesday that incorporates real-time object recognition with moveo control.  I'll post a link here when it's up.

alequeiroz, 2017-12-22:
@jesseweisberg Any news?

jesseweisberg, 2017-12-24:
@alequeiroz sorry for the delay, but I've got something for you now!
I added to the existing **moveo_ros** repo so that you can now use real-time object recognition from a monocular image (ordinary webcam) to perform predefined 'pick and place' trajectories that are specific to the detected object.  Feel free to fork and experiment!
[**code & details**](https://github.com/jesseweisberg/moveo_ros/tree/master/moveo_moveit/scripts)
[**video demo**](https://youtu.be/kkUbyFa2MWc)

liz-miller, 2018-04-23:
@jesseweisberg very cool addition to this project. I'm thinking about starting this project soon & can't wait to interface it with ROS. Random question - roughly how long does it take to print the moveo parts? TIA!

mfkenson, 2018-05-04:
I finally decided to source all parts because you guys make it compatiable with ROS! Thanks for integrating the ROS.

I simply buy the printed parts because I dont have a 3d printer.

jcheng09, 2022-02-21:
Hi Jesse, nice work so far with on the project. I'm following through your simulation workflow now. I'm wondering if you had any luck with implementing the closed-loop feedback control. I'm interested in contributing to its development

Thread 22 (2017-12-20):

Bill of Materials

Amdivns, 2017-12-20:
Can the original poster of this please provide a detailed list of where the items were obtained.

This will enable people in other world regions to obtain equivalents.

This project looks fun, but I can't make heads or tails of half the BOM components. There's so much detail missing...

mfkenson, 2018-05-04:
Refer to #7

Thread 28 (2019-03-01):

4m2 not fitting to gripper parts

DuckY1987, 2019-03-01:
I printed the gripper already and continued with the 4m2 part.

Unfortunately the 4m2 is bigger than the gripper hole distance.

The difference is: ~6mm the Distance between the inner screw holes of the 4m2 is 30mm, the distance between inner screw holes of the gripper is around 23.8mm

DuckY1987, 2019-03-01:
Okay i verified it with the files from here:

Bottom Plate Screw Hole Distance: 24mm
4M2 Screw Hole Distance: 30mm

So basically the mounting points of the gripper assembly and the gear assembly doesn't fit to each other.

The Gripper is already assembled and works.

According to my measurements, the 4m2 part fits to 4m with a 2-3mm tolerance. 48.2mm is the 4m2 printed x2

The hole of 4m2 is rather tight under around 7.9mm might be a bit tight for a 8mm rod.

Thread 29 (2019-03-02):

firmware modifying Configuration.h for different motor/pulley spec

mfkenson, 2019-03-02:
May I know how to derive the value of DEFAULT_AXIS_STEPS_PER_UNIT in Configuration.h  ?

This could help building their arm with different motor/pulley spec.

I found the calculator here.
https://www.prusaprinters.org/calculator/#stepspermmbelt

I don't know how to get the number from the firmware in
https://github.com/BCN3D/BCN3D-Moveo/blob/master/FIRMWARE/Marlin_BCN3D_Moveo/Configuration.h
```
#define DEFAULT_AXIS_STEPS_PER_UNIT   {128.5,45.5,206.8019,760*1.1}  // default steps per mm

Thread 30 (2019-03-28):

Adding Limit Switches to Moveo

Coppertop12, 2019-03-28:
Hello, can someone who has added Limit Switches to their Moveo project please direct me to their work or get in touch? If this is not possible or practical, can someone please explain why?

agneyjadav, 2022-11-09:
Heya coppertop12 if anyone helped you with idea of limit switch, kindly guide us towards it, contact me at agney2001@gmail.com

agneyjadav, 2022-11-09:
> Hello, can someone who has added Limit Switches to their Moveo project please direct me to their work or get in touch? If this is not possible or practical, can someone please explain why?

techsavvyomi, 2024-05-31:
> Hello, can someone who has added Limit Switches to their Moveo project please direct me to their work or get in touch? If this is not possible or practical, can someone please explain why?

Hi, I'm also working on the same arm. Did you find solution to add limit switch to arm ? Thanx in advance.

Coppertop12, 2024-05-31:
Hey! I do not have the files related to this any longer. We did add limit switches and a "homing" program on start up. It was not a difficult modification.

The arm we made, while functional, had several structural issues. The 3D printed parts were too heavy for the motors, even when we sized motors up. Tensioning the belts so they would not slip cracked the 3D prints. We had a different tool attachment however which was much heavier.

Good luck!

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

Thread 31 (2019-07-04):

Don't know how to connect stepper motor drivers TB6560 to Arduino MEGA

dominik098, 2019-07-04:
Hi,
I've just assembled all machanical parts of MOVEO, and now I making wirring. I have an issue, I don't know how to make connection between stepper motor drivers and ardiuno, which PINs of arduino choose to make everything work. I want to control Moveo with software mentioned in User manual (Pronterface).

Ranork, 2019-07-16:
you can find it in google with tb6560 arduino connection

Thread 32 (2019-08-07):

Sensors

AshrafSurour, 2019-08-07:
Sensors or limit switches for homing of each motor haven't been taken into consideration in the design

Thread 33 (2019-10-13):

Problem with stepper motors

Zolmiki2005, 2019-10-13:
HI! I have just finished building BCN3D Moveo. I use Arduino mega 2560 and Marlin fimeware and TB 5050 stepper motor driver. I connect Nema 23 to the ramps 1.4. The Z Axis stepper motors only step into only one direction with the G code programmer. I connect the stepper to the driver, then to the ramps 1.4.
What should I do? Help me, please.

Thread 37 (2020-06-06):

Printing the parts

michaelhotker, 2020-06-06:
do any of the parts require supports at all? I could find anywhere in the manual that said anything about it.

AlfonsoCalero, 2020-06-06:
I don't think you will find an instruction manual at such a low level. There are many parts of the project that will go on your own, although you can always count on people who have carried out the project and will lend you a hand. Regarding the subject of supports, you are supposed to have knowledge about whether an object should use supports or not when printing it.

DominicM1213, 2021-12-12:
Has anyone figured out how to print the 1M1 part? I can't seem to get this lip to print properly.

maedrone, 2021-12-14:
Yo lo. He impreso con soportes y me ha quedado muy bien, sinceramente no utilice ninguna configuración modificada, solo agregue soportes

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

tkircher, 2022-11-05:
It's clear that whoever designed these parts doesn't understand design for 3D printing. Essentially all of these parts require complex supports, when a few small changes would make them require no supports. (For example, tapered hex nut seats instead of flat ones, which is 3D printing design 101)

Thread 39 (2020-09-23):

EXTRUDERS 2

ilimogren, 2020-09-23:
(output status 1
Pasting "DIO" and "-" does not provide a valid preprocessing token)

Located in the configuration.h file
#define EXTRUDERS 1 i

When I want to do EXTRUDERS 2 I get the following error.

I get the same error. I wonder why.
There is a compilation error.
What should I do. Please help me.

jankb89, 2021-03-13:
I got the same issue.
Do you got a solution for this?

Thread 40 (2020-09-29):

forward kinematics and inverse kinematics?

ilimogren, 2020-09-29:
Hi.

I've been dealing for eight months. I cannot calculate the dh sun, forward and inverse kinematics of this robot and get an accurate result. I wonder if anyone calculates. If there is, can you send me an e-mail. huser_er@hotmail.com

aitorrobotica, 2021-06-01:
you got that email? i have the same problem

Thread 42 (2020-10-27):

Stepper Motors

robertall33, 2020-10-27:
Hi there - I am really sorry for being a pain in asking silly questions. I fully understand that this project is about 3-4 years old now, and i think it is the most amazing project to complete ever, and thank you so much for supplying so much information without charge, and letting it be open source.

I am having trouble finding the correct stepper motors. Can someone please point me in the correct direction?

Many thanks, Rob

EBMare, 2021-04-07:
You can find all of the Stepper Motors except the Nema 23.
Use this one instead "Nema 23 stepper 3Nm 4,2A 10mm shaft"

robertall33, 2021-04-07:
Hi there - Its all resolved now, and the robotic arm is almost fully assembled with the exception of sorting out the wiring - Thank you

PROPSMITH, 2021-04-15:
Hi man, I want to know who you are?

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

EBMare, 2021-04-15:
@robertall33 I could help you if you want.

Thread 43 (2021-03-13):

When I configure EXTRUDERS 2, I get an error like this, I wonder why

jankb89, 2021-03-13:
When I configure EXTRUDERS 2, I get an error like this, I wonder why

(exit state 1 "DIO" and "-" are pasted, not a valid preprocessing token)

_Originally posted by @ilimogren in https://github.com/BCN3D/BCN3D-Moveo/issues/26#issuecomment-696885981_

turnfarmer, 2021-06-01:
In Configuration.h define MOTHERBOARD 34

aitorrobotica, 2021-06-01:
Once the board is defined, what I have to do to make it work?

turnfarmer, 2021-06-01:
You upload the firmware on your arduino and in pronterface you can change between the extruders by T0 and T1.

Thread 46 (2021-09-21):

add source files to repo

moedn, 2021-09-21:
First, thanks for making this hardware open source!

I found lots of export files in this repo (PDF, STL etc.). While those are nice for replication, it's quite hard to edit them for modification or further development.

I suggest the following:

- [ ] add source files in native (or at least editable) format to the repo (e.g. `BCN3D Moveo BOM.xlsx` (or even better: as CSV))
  - so others can contribute
- [ ] remove export files (e.g. `BCN3D Moveo BOM.pdf`)
  - git can't handle binaries in a reasonable way; export formats should be either added to a release or created automatically using CI jobs. creating a release and adding those files there would be the easier option, I guess :)

allyouaskfor, 2021-10-09:
The source files are available as SolidWorks files in the CAD directory.

The file you mentioned, BCN3D Moveo BOM.pdf, is a document known as a 'Bill Of Materials' which contains a list of parts required to assemble the end-product.

moedn, 2022-06-23:
whoops sorry for that! seems like this was never an issue than, thanks for the response!

regarding the BoM, I'd still suggest to use an editable format rather than PDF, but that's rather a detail

Closed 2022-06-23.

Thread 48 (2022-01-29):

Electrical or Software Problems

AnOrdinaryUsser, 2022-01-29:
Good Morning,
We are a group of students who are trying to replicate the construction of this robotic arm and we have encountered a problem that we are not able to solve.
We have used the code provided by Marlin to be able to test all the motors, however we have encountered the problem that the two bottom motors that actually raise and lower the arm do not work correctly.
Mostly we encounter this problem when we make use of the arduino code from https://github.com/jesseweisberg/moveo_ros as we do not get the stepper motor to work correctly and it sounds a strange noise.
We are currently using these motors:
https://www.amazon.es/Edred%C3%B3n-pieza-23-Motor-alambre-drehbank/dp/B077XCHLN2/
And we have these two types of controllers:
https://www.amazon.es/DollaTek-bif%C3%A1sico-m%C3%A1x-Controlador-controlador-impresora/dp/B08HQCZ32N
And the TB6560

We have switched from using the TB6560 to the others because these first ones gave less amps than the motor indicated.
We also have the difficulty that inside the controllers there are some switches that we do not know exactly how to configure them, because we do not know what revolutions to use with these motors.

All the other motors work perfectly and these are the only ones that do not give us problems.

Translated with www.DeepL.com/Translator (free version)

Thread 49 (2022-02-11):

BOM  and parts Help.

Timbo515, 2022-02-11:
I’m having trouble finding the correct motors, servos and belts for the stl files provided. I was  hoping to get a detailed list/descriptions of the parts their brand names and where to buy them from. My professor said to look on Amazon but I don’t have enough knowledge to select good parts vs bad parts. Any help would be greatly appreciated.

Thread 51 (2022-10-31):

What pins do I connect to Arduino Mega?

Felip01, 2022-10-31:
I'm kind of a layman on the subject, so if anyone can answer me which pins of the arduino mega I connect the stepper motor to and the others I would be very grateful.

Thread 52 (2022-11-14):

Roughly how long to print this?

JohnAllen, 2022-11-14:
How long does this sucker take to 3d print? I'm guessing a week or so. I only have an Enter Pro V2. Some of the stl files seem bigger than the photos, too.

Navneethpsagar, 2023-06-11:
Hi,

It took us one and a half week to print all the parts for the robotic arm. Depending on your printer configurations you can reduce the time for the printing. We used Prusa i3 MK3S+ and Ender 3 V2.

Hope this helps.
Good luck.

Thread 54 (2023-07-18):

How to connect servo motor?

churc02, 2023-07-18:
Which pin set is the servo motor for the claw mechanism connected to on the RAMPS? And how do you control it in pronterface?

Taha22mohamed, 2023-11-04:
Hi [churc02]
did you find the solution

Closed 2023-08-24.

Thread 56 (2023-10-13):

Steppermotors issue possible workaround?

Irrlich2142, 2023-10-13:
Hey there,

Since the steppermotors are hard to find and if you get them you have to buy them all over the place i thought i take a look and search a bit.
What i found is one shop that sells all whats needed. Only downside is that the voltage is not 2.8-4V like the one in the original Project. But the steppers i found are all 24VDC. Since the power-supply is also 24V its a match. For the drivers there also capable of 24V and  4Amps. Also the signal input that the driver can register is 4.5-5V and 24V. So this should work. But be warned its not as cheep as the steppers in the BOM-List.
The power supply can handle US and EU grid so its universal i guess :D And 14.6A @ 24VDC is perfect since the steppers draw 9.69A. So there is also enough reserve.

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

**Steppers:**
From BOM ID: 1 || Quantity: 1
https://www.omc-stepperonline.com/nema-17-bipolar-1-8deg-45ncm-64oz-in-1-68a-2-8v-42x42x48mm-4-wires-17hs19-1684s1

From BOM ID: 8 || Quantity: 1
https://www.omc-stepperonline.com/nema-17-stepper-motor-bipolar-l-48mm-w-gear-ratio-5-1-planetary-gearbox-17hs19-1684s-pg5

From BOM ID: 9 || Quantity: **2**
https://www.omc-stepperonline.com/nema-23-bipolar-3nm-425oz-in-8mm-diameter-4-2a-57x57x113mm-4-wires-stepper-motor-23hs45-4204s1

From BOM ID: 10 || Quantity: 1
https://www.omc-stepperonline.com/nema-14-bipolar-1-8deg-18ncm-25-5oz-in-0-8a-5-4v-35x35x34mm-4-wires-14hs13-0804s

From BOM ID: 11 || Quantity: 1
https://www.omc-stepperonline.com/nema-17-bipolar-1-8deg-22ncm-31oz-in-1-33a-2-8v-42x42x34mm-4-wires-17hs13-1334s

**Drives:**
From BOM ID: 3 || Quantity: 6
https://www.omc-stepperonline.com/digital-stepper-driver-1-0-4-2a-20-50vdc-for-nema-17-23-24-stepper-motor-dm542t

**Power supply:**
From BOM ID: 4 || Quantity: 1
https://www.omc-stepperonline.com/lrs-350-24-mean-well-350w-24vdc-14-6a-115-230vac-enclosed-switching-power-supply-lrs-350-24

I hope it help some of you.
Please before purchase verify the technical details.

Since i am not 100% sure if its works i bought the list and try it out. But this will take a long time, so don't wait on my input :)

Greetings Irrlicht.

PS: No native English speaker/writer so sorry for that.

SgtCryser, 2024-03-16:
Thank you for this list, it really helped me a lot! Did you already assemble everything? How did it turn out?

Greetings
SgtCryser

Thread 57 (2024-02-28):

PLA temperature

vlak6613, 2024-02-28:
Hello people, I have started building the robot, very cool project.
I printed the parts in PLA. Of course I know that it can tolerate a maximum temperature of 60/70 degrees before it deforms. I must honestly say that I had not estimated that the temperature of the stepper motors could rise so high.

Has anyone also printed the robot using PLA and here is their experience that they would like to share?

Thank you in advance

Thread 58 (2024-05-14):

How do I wire the TB6560 drivers to RAMPS 1.4/How to get pronterface to work?

RoboticPain, 2024-05-14:
I need a wiring guide for the arm. I have assembled the arm and wired it using this diagram:
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
and I would like to know if A. it is correct and B. if so how to get pronterface to work. I uploaded the code to the arduino and tried to use Pronterface but nothing happened.
Thanks!

MateusJFabricio, 2024-09-03:
any update?

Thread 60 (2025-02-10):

Регулятор Мощности

EfremovMikhail, 2025-02-10:
[circuitjs-20250122-194552 Генератор пилы.txt](https://github.com/user-attachments/files/18732285/circuitjs-20250122-194552.txt)
[circuitjs-20250122-195901 Генератор ШИМ.txt](https://github.com/user-attachments/files/18732276/circuitjs-20250122-195901.txt)
[circuitjs-20250122-201943 защита выхода.txt](https://github.com/user-attachments/files/18732283/circuitjs-20250122-201943.txt)
[circuitjs-20250122-202605 пуш-пул.txt](https://github.com/user-attachments/files/18732281/circuitjs-20250122-202605.-.txt)
[circuitjs-20250122-203324 выход с LC.txt](https://github.com/user-attachments/files/18732284/circuitjs-20250122-203324.LC.txt)
[circuitjs-20250123-130805 ОДин NPN.txt](https://github.com/user-attachments/files/18732277/circuitjs-20250123-130805.NPN.txt)
[SCH_Pwm_1_2025-01-09.json](https://github.com/user-attachments/files/18732280/SCH_Pwm_1_2025-01-09.json)
[SCH_Pwm_2_2025-01-10.json](https://github.com/user-attachments/files/18732282/SCH_Pwm_2_2025-01-10.json)
<!-- Failed to upload "ГБОУ Школа 709 - ШИМ регулятор v10.docx" -->
[circuitjs-20241229-145942.txt](https://github.com/user-attachments/files/18732279/circuitjs-20241229-145942.txt)
[circuitjs-20250122-194312 MOSFET - Push-pull.txt](https://github.com/user-attachments/files/18732278/circuitjs-20250122-194312.MOSFET.-.Push-pull.txt)

EfremovMikhail, 2025-02-10:
<!-- Failed to upload "2025_ШИМ.zip" -->

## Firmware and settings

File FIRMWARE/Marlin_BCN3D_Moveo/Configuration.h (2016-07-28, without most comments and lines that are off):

#define CONFIGURATION_H
#include "boards.h"
#define STRING_VERSION_CONFIG_H __DATE__ " " __TIME__ // build date and time
#define STRING_CONFIG_H_AUTHOR "(none, default config)" // Who made the changes.
#define SERIAL_PORT 0
#define BAUDRATE 250000
  #define MOTHERBOARD 33
#define EXTRUDERS 1
#define POWER_SUPPLY 1
#define TEMP_SENSOR_0 0
#define TEMP_SENSOR_1 0
#define TEMP_SENSOR_2 0
#define TEMP_SENSOR_BED 0
#define MAX_REDUNDANT_TEMP_SENSOR_DIFF 10
#define TEMP_RESIDENCY_TIME 10  // (seconds)
#define TEMP_HYSTERESIS 3       // (degC) range of +/- temperatures considered "close" to the target one
#define TEMP_WINDOW     1       // (degC) Window around target to start the residency timer x degC early.
#define HEATER_0_MINTEMP 5
#define HEATER_1_MINTEMP 5
#define HEATER_2_MINTEMP 5
#define BED_MINTEMP 5
#define HEATER_0_MAXTEMP 275
#define HEATER_1_MAXTEMP 275
#define HEATER_2_MAXTEMP 275
#define BED_MAXTEMP 150
#define PIDTEMP
#define BANG_MAX 255 // limits current to nozzle while in bang-bang mode; 255=full current
#define PID_MAX BANG_MAX // limits current to nozzle while PID is active (see PID_FUNCTIONAL_RANGE below); 255=full current
  #define PID_FUNCTIONAL_RANGE 10 // If the temperature difference between the target temperature and the actual temperature
  #define PID_INTEGRAL_DRIVE_MAX PID_MAX  //limit for the integral term
  #define K1 0.95 //smoothing factor within the PID
  #define PID_dT ((OVERSAMPLENR * 10.0)/(F_CPU / 64.0 / 256.0)) //sampling period of the temperature routine
    #define  DEFAULT_Kp 22.2
    #define  DEFAULT_Ki 1.08
    #define  DEFAULT_Kd 114
#define MAX_BED_POWER 255 // limits duty cycle to bed; 255=full current
#define PREVENT_DANGEROUS_EXTRUDE
#define PREVENT_LENGTHY_EXTRUDE
#define EXTRUDE_MINTEMP 170
#define EXTRUDE_MAXLENGTH (X_MAX_LENGTH+Y_MAX_LENGTH) //prevent extrusion of very large distances.
#define ENDSTOPPULLUPS // Comment this out (using // at the start of the line) to disable the endstop pullup resistors
  #define ENDSTOPPULLUP_XMAX
  #define ENDSTOPPULLUP_YMAX
  #define ENDSTOPPULLUP_ZMAX
  #define ENDSTOPPULLUP_XMIN
  #define ENDSTOPPULLUP_YMIN
  #define ENDSTOPPULLUP_ZMIN
const bool X_MIN_ENDSTOP_INVERTING = true; // set to true to invert the logic of the endstop.
const bool Y_MIN_ENDSTOP_INVERTING = true; // set to true to invert the logic of the endstop.
const bool Z_MIN_ENDSTOP_INVERTING = true; // set to true to invert the logic of the endstop.
const bool X_MAX_ENDSTOP_INVERTING = true; // set to true to invert the logic of the endstop.
const bool Y_MAX_ENDSTOP_INVERTING = true; // set to true to invert the logic of the endstop.
const bool Z_MAX_ENDSTOP_INVERTING = true; // set to true to invert the logic of the endstop.
#if defined(COREXY) && !defined(DISABLE_MAX_ENDSTOPS)
  #define DISABLE_MAX_ENDSTOPS
#endif
#define X_ENABLE_ON 0
#define Y_ENABLE_ON 0
#define Z_ENABLE_ON 0
#define E_ENABLE_ON 0 // For all extruders
#define DISABLE_X false
#define DISABLE_Y false
#define DISABLE_Z false
#define DISABLE_E false // For all extruders
#define DISABLE_INACTIVE_EXTRUDER false //disable only inactive extruders and keep active extruder enabled
#define INVERT_X_DIR true    // for Mendel set to false, for Orca set to true
#define INVERT_Y_DIR false    // for Mendel set to true, for Orca set to false
#define INVERT_Z_DIR true     // for Mendel set to false, for Orca set to true
#define INVERT_E0_DIR false   // for direct drive extruder v9 set to true, for geared extruder set to false
#define INVERT_E1_DIR false    // for direct drive extruder v9 set to true, for geared extruder set to false
#define INVERT_E2_DIR false   // for direct drive extruder v9 set to true, for geared extruder set to false
#define X_HOME_DIR -1
#define Y_HOME_DIR -1
#define Z_HOME_DIR -1
#define min_software_endstops false // If true, axis won't move to coordinates less than HOME_POS.
#define max_software_endstops false  // If true, axis won't move to coordinates greater than the defined lengths below.
#define X_MAX_POS 205
#define X_MIN_POS 0
#define Y_MAX_POS 205
#define Y_MIN_POS 0
#define Z_MAX_POS 200
#define Z_MIN_POS 0
#define X_MAX_LENGTH (X_MAX_POS - X_MIN_POS)
#define Y_MAX_LENGTH (Y_MAX_POS - Y_MIN_POS)
#define Z_MAX_LENGTH (Z_MAX_POS - Z_MIN_POS)
#define Z_PROBE_REPEATABILITY_TEST  // If not commented out, Z-Probe Repeatability test will be included if Auto Bed Leveling is Enabled.
#define MANUAL_X_HOME_POS 0
#define MANUAL_Y_HOME_POS 0
#define MANUAL_Z_HOME_POS 0
#define NUM_AXIS 4 // The axis order in all axis related arrays is X, Y, Z, E
#define HOMING_FEEDRATE {50*60, 50*60, 4*60, 0}  // set the homing speeds (mm/min)
#define DEFAULT_AXIS_STEPS_PER_UNIT   {128.5,45.5,206.8019,760*1.1}  // default steps per mm
#define DEFAULT_MAX_FEEDRATE          {500, 500, 500, 25}    // (mm/sec)
#define DEFAULT_MAX_ACCELERATION      {60, 100, 5, 10000}    // X, Y, Z, E maximum start speed for accelerated moves. E default values are good for Skeinforge 40+, for older versions raise them a lot.
#define DEFAULT_ACCELERATION          500    // X, Y, Z and E max acceleration in mm/s^2 for printing moves
#define DEFAULT_RETRACT_ACCELERATION  3000   // X, Y, Z and E max acceleration in mm/s^2 for retracts
#define DEFAULT_XYJERK                20.0    // (mm/sec)
#define DEFAULT_ZJERK                 0.4     // (mm/sec)
#define DEFAULT_EJERK                 5.0    // (mm/sec)
#define CUSTOM_M_CODES
  #define CUSTOM_M_CODE_SET_Z_PROBE_OFFSET 851
  #define Z_PROBE_OFFSET_RANGE_MIN -15
  #define Z_PROBE_OFFSET_RANGE_MAX -5
#define EEPROM_SETTINGS
#define PLA_PREHEAT_HOTEND_TEMP 180
#define PLA_PREHEAT_HPB_TEMP 70
#define PLA_PREHEAT_FAN_SPEED 255   // Insert Value between 0 and 255
#define ABS_PREHEAT_HOTEND_TEMP 240
#define ABS_PREHEAT_HPB_TEMP 100
#define ABS_PREHEAT_FAN_SPEED 255   // Insert Value between 0 and 255
#define SOFT_PWM_SCALE 0
#define NUM_SERVOS 3 // Servo index starts with 0 for M280 command
#define FILAMENT_SENSOR_EXTRUDER_NUM	0  //The number of the extruder that has the filament sensor (0,1,2)
#define MEASUREMENT_DELAY_CM			14  //measurement delay in cm.  This is the distance from filament sensor to middle of barrel
#define DEFAULT_NOMINAL_FILAMENT_DIA  3.0  //Enter the diameter (in mm) of the filament generally used (3.0 mm or 1.75 mm) - this is then used in the slicer software.  Used for sensor reading validation
#define MEASURED_UPPER_LIMIT          3.30  //upper limit factor used for sensor reading validation in mm
#define MEASURED_LOWER_LIMIT          1.90  //lower limit factor for sensor reading validation in mm
#define MAX_MEASUREMENT_DELAY			20  //delay buffer size in bytes (1 byte = 1cm)- limits maximum measurement delay allowable (must be larger than MEASUREMENT_DELAY_CM  and lower number saves RAM)
#define DEFAULT_MEASURED_FILAMENT_DIA  DEFAULT_NOMINAL_FILAMENT_DIA  //set measured to nominal initially
#include "Configuration_adv.h"
#include "thermistortables.h"

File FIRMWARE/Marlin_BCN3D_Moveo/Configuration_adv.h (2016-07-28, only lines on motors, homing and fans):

#define CONTROLLERFAN_PIN -1 //Pin used for the fan to cool controller (-1 to disable)
#define EXTRUDER_0_AUTO_FAN_PIN   -1
#define EXTRUDER_1_AUTO_FAN_PIN   -1
#define EXTRUDER_2_AUTO_FAN_PIN   -1
#define ENDSTOPS_ONLY_FOR_HOMING // If defined the endstops will only be used for homing
#define X_HOME_RETRACT_MM 5
#define Y_HOME_RETRACT_MM 5
#define Z_HOME_RETRACT_MM 2
#define MICROSTEP1 LOW,LOW
#define MICROSTEP2 HIGH,LOW
#define MICROSTEP4 LOW,HIGH
#define MICROSTEP8 HIGH,HIGH
#define MICROSTEP16 HIGH,HIGH
#define MICROSTEP_MODES {16,16,16,16,16} // [1,2,4,8,16]
#define DIGIPOT_MOTOR_CURRENT {135,135,135,135,135} // Values 0-255 (RAMBO 135 = ~0.75A, 185 = ~1A)
#define DIGIPOT_I2C_MOTOR_CURRENTS {1.0, 1.0, 1.0, 1.0, 1.0, 1.0, 1.0, 1.0}

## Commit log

2016-07-28 Add files to Repo!
    First operating version of the BCN3D Moveo
    [1M1.STL, 1M1B.SLDPRT, 1M2.STL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]
2016-07-28 added missing file
    [3M1.STL]
2016-08-02 Added missing Txxx files
    [T4M1E.stl]
2016-08-02 Added missing Txx files
    [T2M1BD.stl, T2M1BI.stl]
2016-10-03 Updated BOM file and changed to PDF file
    [BCN3D Moveo BOM.xlsx]
